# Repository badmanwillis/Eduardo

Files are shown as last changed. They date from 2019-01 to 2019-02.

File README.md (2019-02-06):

# Eduardo
Eduardo the hair combing robot. An assistive robot arm prototype featuring a passive compliant end effector. A University of Plymouth MEng Robotics ROCO504 project.

Olly Smith and Sam White 2018. Module lead by Martin F Stoelen.

## About Eduardo

People with temporary or permanent disabilities often struggle to perform daily tasks, and as a result, this loss of agency can cause undue emotional distress. For this project, we present “Eduardo”; a prototype robot arm designed with the intention of returning autonomy to the user. In particular, we utilise a passive compliant element in the end effector, to greatly simplify the control of the arm, and ensure the safety of the user during physical interaction. As a demonstration of the prototype, we have programmed the arm to comb hair, although we envision a wider range of potential applications.

From our research, this may well be the first prototype of assistive robot that features a passive compliant end effector. It was built in under three months, by two people, on a budget of £70. As a result, shortcuts were taken for the sake of creating a functioning prototype, and much of the work here does not adhere to best practices.

Sam White was responsible for the design and manufacture of the arm. This was his first project attempted using Fusion360. Parts were rapidly protoyped and developed iterativley, through 3D printing. Additional work included parts procurement, sensor testing, and building a wheatstone bridge for the flex sensor.

Olly Smith was responsible for the ROS software and c++ microcontroller code for the arm. This was his first project attempted using ROS. Addtional work included advising Sam on designing parts for 3D printing - having built an ANET A8, and creating a custom control board for the stepper drivers and servo power rails.

Finally, the robot arm itself lends itself to further use as a development platform at the university for research projects. The large workspace (including the vertical prismatic element of the pedestal), well executed construction of the arm using low cost components, and open source software, makes the arm a viable candidate for students to use in their own research projects, continuing the research we present, and for their own ideas.

## Media
imgur album

[Rough cut of a showcase video for the project](https://www.youtube.com/watch?v=7iySw0dwJq0)

## ROS packages

The software was developed on a Ubuntu 16.04 LTS machine, using ROS-Kinetic. You'll need to setup a catkin workspace, and put the packages into the src folder.

#### Setup a workspace
[Creating a Catkin Workspace](http://wiki.ros.org/catkin/Tutorials/create_a_workspace)

Open a terminal (should default to the home directory):
 
create the folders
> mkdir -p ~/eduardo_ws/src

navigate to the root folder
> cd ~/eduardo_ws/

make the workspace using the catkin_make command
> catkin_make

#### Add the packages
[Creating a ROS Package](http://wiki.ros.org/catkin/Tutorials/CreatingPackage)

Move the two folders "sam" and "sam_moveit_config" into the src folder.

Make sure you are still in the root folder "eduardo_ws" using the "cd" and "cd .." commands

re-build the workspace

> catkin_make

"source the workspace". This means adding the workspace to the ROS enviroment by sourcing the generated setup file.

> source devel/setup.bash 

### sam

This package features the Fusion360 stl files for the the arm links, as well as the samcad.urdf (Universal Robot Description Format) file. It can be used to visualize the arm in Rviz, and control the joints via GUI sliders.

#### usage
Navigate to your workspace

> cd ros_ws

Source your workspace

> source devel/setup.bash

run the demo

> roslaunch sam arm_display.launch 

Wait for Rviz to load, then use the joint_state_publisher window sliders to play about with the arm.

### sam_moveit_config

The [moveit!](https://moveit.ros.org/) configuration package for the samcad.urdf. Unfortunatley it doesn't support path planning right now, as the deafult kinematics solvers only support 6DOF arms. I've tried adding a dummy link, which should fix the issue with a bit more work.

#### usage
Navigate to your workspace

> cd ros_ws

Source your workspace

> source devel/setup.bash

run the demo

> roslaunch sam_moveit_config demo.launch

Wait for Rviz to load, tick the "Allow Approx IK Solutions" option in the Planning tab. Drag the arm Query Start State and Query Goal State (found under Planning Request), and use the commands within the Planning tab to have moveit perform path planning and simulate the arms movement.

## Motor control code

A [ST-Nucleo-F429ZI Microcontroller](https://os.mbed.com/platforms/ST-Nucleo-F429ZI/) was used to control the stepper and servo motors, as well as read the the flex sensor value.

### nucleo_code.cpp
Most complete working code. The start and end postions of the arm are hard coded, and upon excution (trigger from a ros terminal command).

### demo_code.cpp
A version of nucleo_code.cpp with all superfluous code removed. Used to demostrate the arm on the demostration day. See the simple combing demonstration for usage.

### master_code.cpp
The most complete code in developement. Unfinished. Designed to by used by both the arm_display.launch program (sam) to allow remote control from the computer, using the GUI sliders. Also for use by the demo.launch (sam_moveit_config) program to execute path planning between given positions.

#### Simple combing demonstration
For the project showcase day a greatly simplified version of the code (demo_code.cpp) was run, to ensure a successful demonstration.
**_WARNING_. The arm will move to a starting position as soon as the microcontroller and PSU are on.**

In a terminal.
> roscore

Open a new terminal tab (Ctrl + shift + T). Then run the ros serial command to connect the Ubuntu machine to the Microcontroller. If you forgot to plug the microcontroller into the computer first, that's okay, I've done it as well.
> rosrun rosserial_python serial_node.py _port:=/dev/ttyACM0 _baud:=115200

Have the arm execute a hard coded path. Place a head of hair in the path of the arm to have it combed.
> rostopic pub toggle_execute std_msgs/Empty --once

#### Other useful commands
These have proven useful in development.

List the current ROS topics
> rostopic list

Print the updating values of the joints of the arm.
> rostopic echo joint_states

Generate a ROS computation graph to visualize the topics and nodes.
> rqt_graph

## Further improvements
There is no shortage of improvements to be made to this project, and we hope to see the continued development of this arm in the future.

### Research
- Attempt combing on the sides of the hair, and potentially to style the hair.
- Create an end effector using an antagonstic pair, for variable compliance.
- Experiment with other means of helping a person with upper body impairments. Examples include washing, feeding, clothing.

### Safety
- Add microswitches to the prismatic gantry and shoulder revolute joints as endstops. Like a 3D printer.
- Add padding to the arm itself, potentially with sensors or microswithces to detect a collision.
- Add a big red emergency stop button.

### Design and construction
- An improved attachment method, which still allows for end effectors to be easily swapped. The current end effector attachement is friction fit, and can become loose over time.
- Create a better mount for the PSU and motor control board. Currently an elastic band is doing a fantastic job, but it's not ideal.
- Addition of a belt tensioner for the  shoulder joint would make keeping the belt taught much simpler.
- Replacing servo plugs with molex connectors. Current connects have no locking mechanism and can occasionally be pulled out when prismatic joint is at it's extremes.
- A comb piece design with less sharp prongs should be considered. Adjust as necessary for comfort.

### Control Software
- Intergrate a sensor to establish the cartesian position of the users head. This was attempted using a KinectV2, and a custom stereo camera system, but was abandoned due to time.
- Intergate the Stepper motor for the pedestal, adding a vertical prismatic joint to the URDF.

#### Moveit!
- Create a custom kinematics solver plugin, or use IKFast, or Trac-IK.
- Define controllers. A YAML file of the joints. See sam_moveit_config > config.
- Use python scripting to control the arm. See the [Move Group Python Interface](http://docs.ros.org/kinetic/api/moveit_tutorials/html/doc/move_group_python_interface/move_group_python_interface_tutorial.html) tutorial.

- Create a launch file / bash script that launches the whole enviroment from single terminal command

### Fun ideas
- Implement voice synthesis, give it an old-timey british barber voice, a bit like Codsworth from Fallout 4.
- Create an end effector of a silicon mould of a hand, to high-five passers by.

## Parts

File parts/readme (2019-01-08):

Parts list from Ooznest and step(.stp) CAD files for all printed parts necessary to the build of the arm.  

'Parts List' is a text document including parts bought, in what quiantity and a link to the page from which they were purchased. 

'Eduardo Step Files' is a set of step files for the CAD design.

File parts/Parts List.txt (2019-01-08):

Official List of Parts on OpenBuild
https://openbuilds.com/builds/nema-17-belt-and-pinion-system.7499/

V-Slot Gantry Plate (x1)
https://ooznest.co.uk/product/v-slot-gantry-plate/

NEMA17 Motor Mounting Plate (x1)
https://ooznest.co.uk/product/nema17-motor-mounting-plate/

Delrin Dual V Wheel Kit (x4)
https://ooznest.co.uk/product/delrin-dual-v-wheel/

Tee Nuts (x10)
https://ooznest.co.uk/product/tee-nuts/

GT2 Pulley 20T (x2)
https://ooznest.co.uk/product/gt2-pulleys/

GT2 Open Timing Belt 
https://ooznest.co.uk/product/gt2-open-timing-belt-per-metre/

V-Slot Linear Rail – 20x80x1000mm (x1)
https://ooznest.co.uk/product/v-slot-linear-rail-20x80mm-cut-to-size/

M3 Socket Head Bolts (x8)
https://ooznest.co.uk/product/m3-socket-head-bolts/

M5 Low Profile Bolts (x8)
https://ooznest.co.uk/product/low-profile-m5-bolts/

Aluminium Spacers (x2)
https://ooznest.co.uk/product/aluminium-spacer/

Eccentric Spacer (x2)
https://ooznest.co.uk/product/eccentric-spacer/

Double Tee Nut (x2)
https://ooznest.co.uk/product/double-tee-nuts/

Total at time of ordering - £73.86

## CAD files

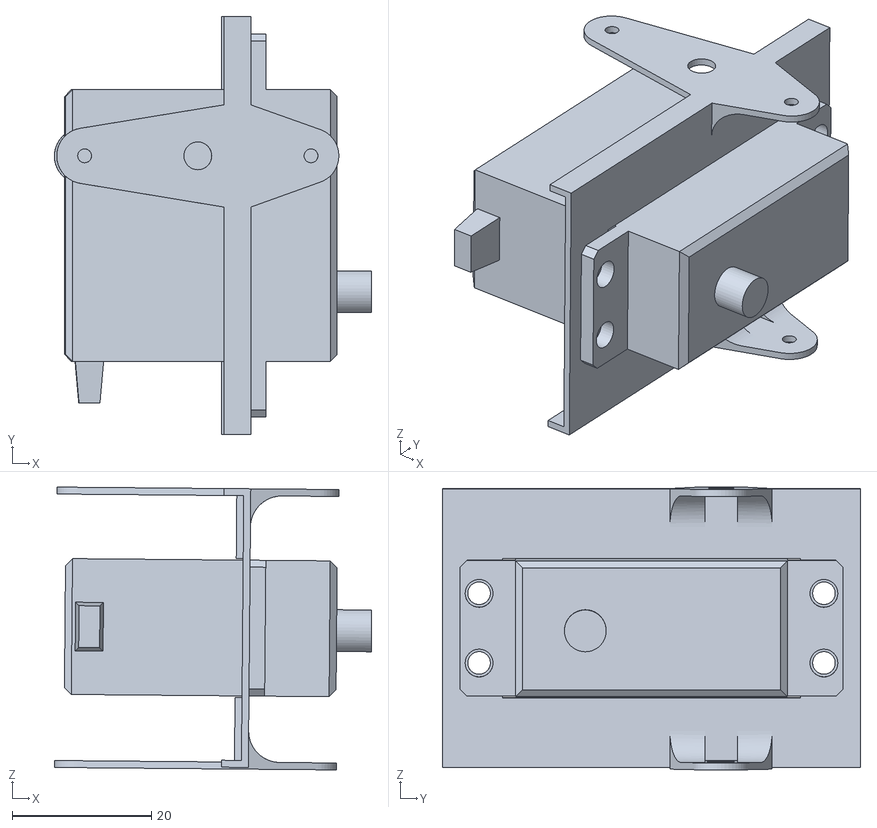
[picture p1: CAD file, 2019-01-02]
sam/src/stls/03_Wrist Servo.stl
45.5 x 60.0 x 40.6

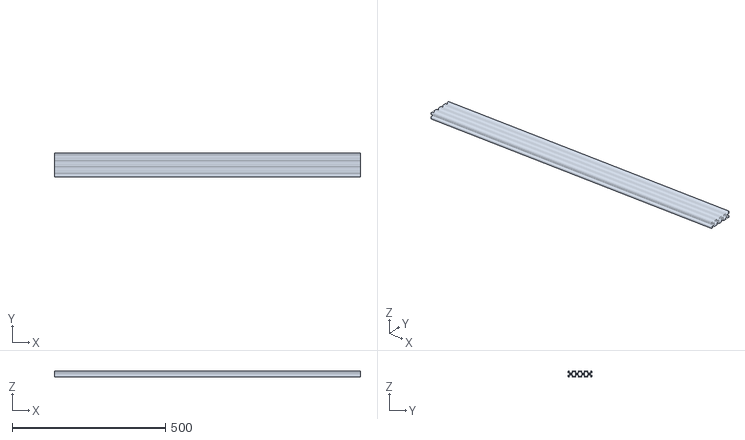
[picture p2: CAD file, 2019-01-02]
sam/src/stls/07_Rail.stl
1000.0 x 80.0 x 20.0

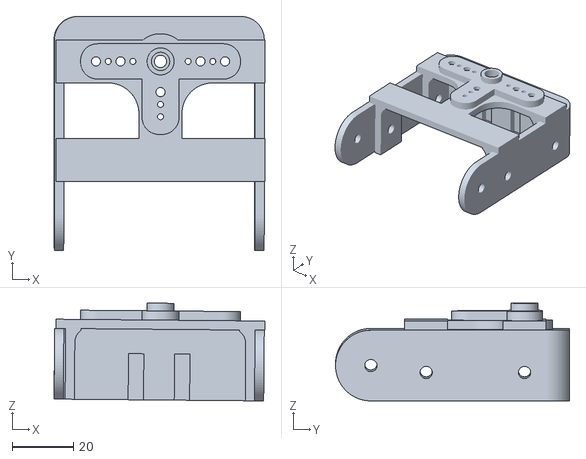
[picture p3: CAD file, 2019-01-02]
sam/src/stls/02_End Effector Front.stl
68.6 x 76.1 x 31.8

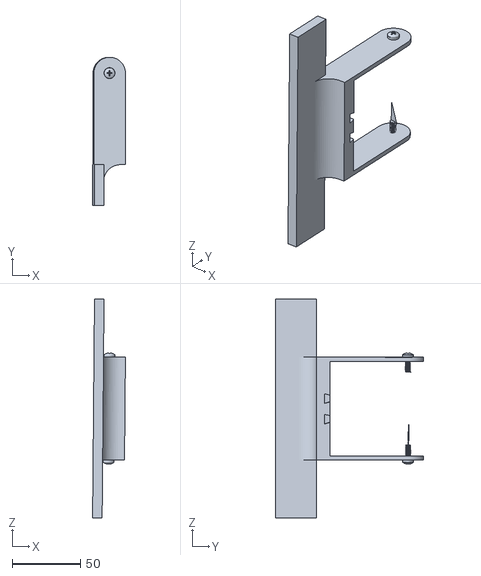
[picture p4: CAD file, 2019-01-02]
sam/src/stls/01_End Effector Top.stl
24.0 x 108.5 x 160.1

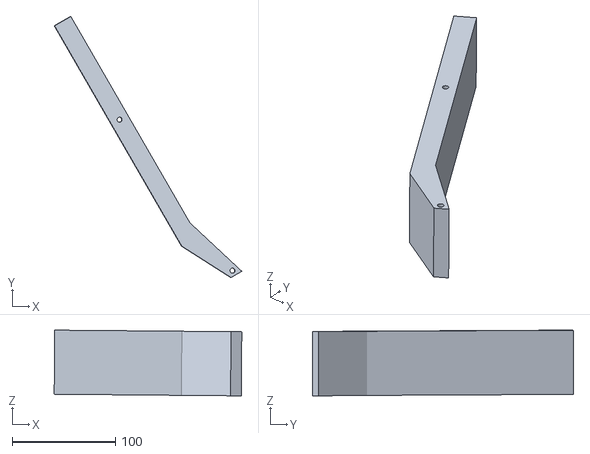
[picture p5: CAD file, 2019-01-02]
sam/src/stls/04_Forearm.stl
181.4 x 252.3 x 63.6

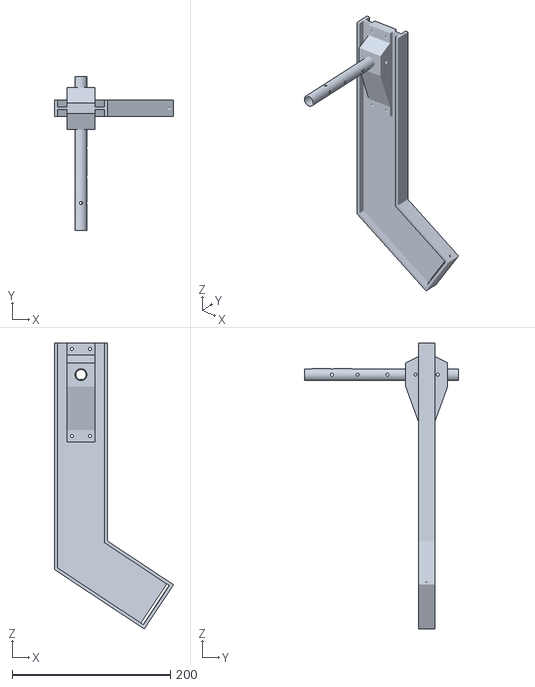
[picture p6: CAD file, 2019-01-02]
sam/src/stls/05_Upper Arm.stl
150.4 x 195.0 x 361.1

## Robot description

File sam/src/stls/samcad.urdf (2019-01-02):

<?xml version="1.0"?>

<!--
Olly Smith & Sam White 2018

Loading in fusion360 parts to create a URDF model of the robot.

-->

<robot name="eduardo">

<!--
2.1.19
fixing the kinematics via a dummy base link
https://groups.google.com/forum/#!topic/moveit-users/kQXU5NYgOF8
-->

  <link name="base_footprint">
    <visual>
      <origin rpy="0 0 0" xyz="0 0 0"/>
      <geometry>
        <box size="0.001 0.001 0.001"/>
      </geometry>
    </visual>
  </link>

  <link name="base_link">
    <visual>
      <geometry>
        <mesh filename="file:/home/olly/ros_ws/src/sam/src/stls/07_Rail.stl" scale="0.001 0.001 0.001"/>
      </geometry>
      <origin rpy = "1.57 0 0" xyz = "0 0 0.04"/>
    </visual>
  </link>


  <joint name="base_footprint_joint" type="fixed">
    <origin rpy="0 0 0" xyz="0 0 0"/>
    <child link="base_link"/>
    <parent link="base_footprint"/>
  </joint>

  <link name="shoulder">
    <visual>
      <geometry>
        <mesh filename="file:/home/olly/ros_ws/src/sam/src/stls/06_GantryPlate.stl" scale="0.001 0.001 0.001"/>
      </geometry>
      <origin rpy = "1.57 0 0" xyz = "0 0 0.04"/>
    </visual>
  </link>

  <joint name="base_to_shoulder" type="prismatic">
    <axis xyz="1 0 0"/>
    <limit effort="1000" lower="-0.45" upper="0.45" velocity="0.1"/>
    <parent link="base_link"/>
    <child link="shoulder"/>
    <origin rpy = "0 0 0" xyz = "0 0 0"/>
  </joint>

  <link name="upper_arm">
    <visual>
      <geometry>
        <mesh filename="file:/home/olly/ros_ws/src/sam/src/stls/05_Upper Arm.stl" scale="0.001 0.001 0.001"/>
      </geometry>
      <origin rpy = "1.57 0 0" xyz = "0 0 0"/>
    </visual>
  </link>


  <joint name="shoulder_upper_arm" type="revolute">
    <axis xyz="0 0 1"/>
    <limit effort="1000" lower="-1" upper="1" velocity="0.1"/>
    <parent link="shoulder"/>
    <child link="upper_arm"/>
    <origin rpy = "0 0 0" xyz = "0 0.043 0"/>
  </joint>

  <link name="lower_arm">
    <visual>
      <geometry>
        <mesh filename="file:/home/olly/ros_ws/src/sam/src/stls/04_Forearm.stl" scale="0.001 0.001 0.001"/>
      </geometry>
      <origin rpy = "0 0 0" xyz = "0 0 0"/>
    </visual>
  </link>

  <joint name="upper_lower_arm" type="revolute">
    <axis xyz="0 0 1"/>
    <limit effort="1000" lower="0.3" upper="2.5" velocity="0.1"/>
    <parent link="upper_arm"/>
    <child link="lower_arm"/>
    <origin rpy = "1.0 1.57 0" xyz = "0.093 0.29 0.1377"/>
  </joint>



  <link name="comb_upper">
    <visual>
      <geometry>
        <mesh filename="file:/home/olly/ros_ws/src/sam/src/stls/03_Wrist Servo.stl" scale="0.001 0.001 0.001"/>
      </geometry>
      <origin rpy = "0 0 0" xyz = "0 0 0"/>
    </visual>
  </link>

  <joint name="lower_arm_hand" type="revolute">
    <axis xyz="0 0 1"/>
    <limit effort="1000" lower="-0.85" upper="1.6" velocity="0.1"/>
    <parent link="lower_arm"/>
    <child link="comb_upper"/>
    <origin rpy = "0 0 0" xyz = "0.108 -0.144 0"/>
  </joint>


  <link name="comb">
    <visual>
      <geometry>
        <mesh filename="file:/home/olly/ros_ws/src/sam/src/stls/02_End Effector Front.stl" scale="0.001 0.001 0.001"/>
      </geometry>
      <origin rpy = "0 0 0" xyz = "0 0 0"/>
    </visual>
  </link>

  <joint name="comb" type="revolute">
    <axis xyz="0 0 1"/>
    <limit effort="1000" lower="-1.6" upper="1.6" velocity="0.1"/>
    <parent link="comb_upper"/>
    <child link="comb"/>
    <origin rpy = "0 -1.57 0" xyz = "0.0224 -0.0195 0"/>
  </joint>


  <link name="comb_end">
    <visual>
      <geometry>
        <mesh filename="file:/home/olly/ros_ws/src/sam/src/stls/01_End Effector Top.stl" scale="0.001 0.001 0.001"/>
      </geometry>
      <origin rpy = "0 0 0" xyz = "0 0 0"/>
    </visual>
  </link>

  <joint name="comb_end" type="revolute">
    <axis xyz="0 0 1"/>
    <limit effort="1000" lower="0" upper="1.6" velocity="0.1"/>
    <parent link="comb"/>
    <child link="comb_end"/>
    <origin rpy = "0 1.57 0" xyz = "0.0032 -0.049387 -0.01975"/>
  </joint>











































</robot>

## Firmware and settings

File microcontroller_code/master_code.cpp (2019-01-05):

#include "mbed.h"
#include "rtos.h"
#include "Servo.h"
#include "ros.h"
#include <std_msgs/Float32.h>
#include <ros.h>
#include <std_msgs/Empty.h>
#include <sensor_msgs/JointState.h>

Serial pc(USBTX, USBRX);
ros::NodeHandle nh;

DigitalOut green(LED1); //Green LED Used to indicate when nucleo has finished executing a movement.
DigitalOut blue(LED2); //Blue LED Used to indicate that the robot is moving.
DigitalOut red(LED3); // Red LED

//Stepper Motors
DigitalOut rev_step(D4); // toggle high to step one increment. //D5 on my nucleo board has a jumper pin stuck in it.
DigitalOut rev_direction(D7); //1 for forwards, 0 for backwards
DigitalOut pris_step(D6);
DigitalOut pris_direction(D8); //1 for forwards, 0 for backwards

//Servo Motors
Servo elbow(D11);
Servo wrist(D10);
Servo hand(D9);

// Flex sensor
AnalogIn   flex_A0(A0);
AnalogIn   flex_A1(A1);
float flex_delta;
float flex_total;
float flex_1;
float flex_2;
float flex_3;
float flex_4;
float flex_5;
float flex_6;
float flex_7;
float flex_8;
float flex_9;
float flex_10;


// goal positions for Servo motors, to be set by the joint_states publisher.
float elbow_goal;
float wrist_goal;
float hand_goal;


// goal positions for Stepper motors, to be set by the joint_states publisher.
int revolute_goal;
int prismatic_goal;

// Current stepper positions
int revolute_pos;
int prismatic_pos;

Thread thread;

void messageCb(const std_msgs::Empty& toggle_msg);
void messageCb1(const std_msgs::Empty& toggle_msg);


ros::Subscriber<std_msgs::Empty> sub("toggle_led", &messageCb);
ros::Subscriber<std_msgs::Empty> sub1("toggle_execute", &messageCb1);
std_msgs::Float32 flex_msg;
ros::Publisher flex("flex", &flex_msg);

 
void ros_thread() {
    while (true) {
        //red = !red;
        //Thread::wait(1000);
        nh.spinOnce();
        Thread::wait(1);
    }
}

// callback messages: Toggle LED
void messageCb(const std_msgs::Empty& toggle_msg){
    green= !green;   // blink the led
}
// callback messages: EXECUTE
int execute = 0;
void messageCb1(const std_msgs::Empty& toggle_msg){
    execute = 1;
    
    green = !green;   // blink the led
}

// joint_state subscriber
#include <sensor_msgs/JointState.h>
void jointCb(const sensor_msgs::JointState& cmd_msg)
{
    //str_msg.data = hello;
    //chatter.publish( &str_msg ); 
    //myled = !myled;
    
    // Code here to take the joint_states and put them into a means that can be used by the code to move the arm.
    // Splitting the input data, putting data into variables eg:
    
    // hand_goal = joint_states[element of array for hand joint state];
    
}
ros::Subscriber<sensor_msgs::JointState> sub2("joint_states", &jointCb);


int main() {
    
    // ROS setup
    nh.initNode();
    pc.baud (115200);
    nh.subscribe(sub);
    nh.subscribe(sub1);
    nh.subscribe(sub2); //joint_states
    nh.advertise(flex);
    thread.start(ros_thread);
    
    // initialise stepper positions to 0
    prismatic_pos =0;
    revolute_pos =0;
    //initialise servo positions to 0
    elbow   =0.5;
    wrist   =0.5;
    hand    =0.7;
    
    int step_rate = 1; // the wait time, in us. Essentially speed control for all motors.
    
    // TESTING goal positions
    prismatic_goal  =4000;
    revolute_goal   =0;
    elbow_goal      =0.5;
    wrist_goal      =0.5;
    hand_goal       =0.7;
    
    // Servo goal tolerances
    float elbow_plus = elbow_goal + 0.01f;
    float elbow_minus = elbow_goal - 0.01f;
    
    float wrist_plus = wrist_goal + 0.01f;
    float wrist_minus = wrist_goal - 0.01f;
    
    float hand_plus = hand_goal + 0.01f;
    float hand_minus = hand_goal - 0.01f;
    
    // Flex sensor upper and lower thresholds (too much force, too little force)
    float flex_high =  0.002;
    float flex_low = 0.001;
    
    
    
    while(1){
        

        while (execute == 1) {
            
            // FLEX SAMPLING
            flex_1 = flex_A0 - flex_A1;
            Thread::wait(1);
            flex_2 = flex_A0 - flex_A1;
            Thread::wait(1);
            flex_3 = flex_A0 - flex_A1;
            Thread::wait(1);
            flex_4 = flex_A0 - flex_A1;
            Thread::wait(1);
            flex_5 = flex_A0 - flex_A1;
            Thread::wait(1);
            flex_6 = flex_A0 - flex_A1;
            Thread::wait(1);
            flex_7 = flex_A0 - flex_A1;
            Thread::wait(1);
            flex_8 = flex_A0 - flex_A1;
            Thread::wait(1);
            flex_9 = flex_A0 - flex_A1;
            Thread::wait(1);
            flex_10 = flex_A0 - flex_A1;
        
            
            flex_total = flex_1 + flex_2 + flex_3 + flex_4 + flex_5 + flex_6 + flex_7 + flex_8 + flex_9 + flex_10;
            flex_delta = flex_total / 10;
            
            flex_delta = fabs(flex_delta);
            
            if(flex_delta < flex_low){
                // TO LOW
                red=1;
                blue=0;
                elbow = elbow - 0.003f;
                wait_ms(step_rate);
                red=0;
            } else if(flex_delta > flex_high){
                // TOO HIGH
                red=0;
                blue=1;
                elbow = elbow + 0.003f;
                wait_ms(step_rate);
                blue = 0;
            }
            

            // Check all motors have reached goal positions. IDGAF about how long the condition statement is.
            if(prismatic_pos == prismatic_goal && revolute_pos == revolute_goal && elbow <= elbow_plus && elbow >= elbow_minus && wrist <= wrist_plus && wrist >= wrist_minus && hand <= hand_plus && hand >= hand_minus){
                // goal reached
                green = 0;
                execute = 0;
                
                //reset positions, may not be needed with moveit intergration.
                prismatic_pos = 0;
                revolute_pos = 0;
            }  
            
            // ELBOW
            if(elbow < elbow_goal){
                blue=1;
                elbow = elbow + 0.01f;
                wait_us(step_rate);
                blue=0;
            } else if(elbow > elbow_goal){
                blue=1;
                elbow = elbow - 0.01f;
                wait_us(step_rate);
                blue=0;
            }
            
           
            // WRIST
            if(wrist < wrist_goal){
                blue=1;
                wrist = wrist + 0.01f;
                wait_us(step_rate);
                blue=0;
            } else if(wrist > wrist_goal){
                blue=1;
                wrist = wrist - 0.01f;
                wait_us(step_rate);
                blue=0;
            }
        
            // HAND
            if(hand < hand_goal){
                blue=1;
                hand = hand + 0.01f;
                wait_us(step_rate);
                blue=0;
            } else if(hand > hand_goal){
                blue=1;
                hand = hand - 0.01f;
                wait_us(step_rate);
                blue=0;
            }
            
            // PRISMATIC
            if(prismatic_pos < prismatic_goal){
                // step fwd 1
                pris_direction = 1;
                
                // STEP
                blue=1;
                pris_step = 1;
                wait_us(step_rate);
                blue=0;
                pris_step = 0;
                wait_us(step_rate);
                // Increment current position
                prismatic_pos +=1;
                 
            } else if(prismatic_pos > prismatic_goal){
                // step back 1
                pris_direction = 0;
                
                // STEP
                blue=1;
                pris_step = 1;
                wait_us(step_rate);
                blue=0;
                pris_step = 0;
                wait_us(step_rate);
                // Decrement current position
                prismatic_pos -=1;
                
            } else if(revolute_pos == revolute_goal){
                // to keep the speeds roughly the same
                wait_us(step_rate);
                wait_us(step_rate);
            }
            
            // REVOLUTE
            if(revolute_pos < revolute_goal){
                // step fwd 1
                rev_direction = 1;
                
                // STEP
                blue=1;
                rev_step = 1;
                wait_us(step_rate);
                blue=0;
                rev_step = 0;
                wait_us(step_rate);
                // Increment current position
                revolute_pos +=1;
                 
            } else if(revolute_pos > revolute_goal){
                // step back 1
                rev_direction = 0;
                
                // STEP
                blue=1;
                rev_step = 1;
                wait_us(step_rate);
                blue=0;
                rev_step = 0;
                wait_us(step_rate);
                // Decrement current position
                revolute_pos -=1;
                
            } else if(revolute_pos == revolute_goal){
                // to keep the speeds roughly the same
                wait_us(step_rate);
                wait_us(step_rate);
            }
            
        }
    }
    
}

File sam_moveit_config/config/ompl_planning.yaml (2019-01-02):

planner_configs:
  SBL:
    type: geometric::SBL
    range: 0.0  # Max motion added to tree. ==> maxDistance_ default: 0.0, if 0.0, set on setup()
  EST:
    type: geometric::EST
    range: 0.0  # Max motion added to tree. ==> maxDistance_ default: 0.0, if 0.0 setup()
    goal_bias: 0.05  # When close to goal select goal, with this probability. default: 0.05
  LBKPIECE:
    type: geometric::LBKPIECE
    range: 0.0  # Max motion added to tree. ==> maxDistance_ default: 0.0, if 0.0, set on setup()
    border_fraction: 0.9  # Fraction of time focused on boarder default: 0.9
    min_valid_path_fraction: 0.5  # Accept partially valid moves above fraction. default: 0.5
  BKPIECE:
    type: geometric::BKPIECE
    range: 0.0  # Max motion added to tree. ==> maxDistance_ default: 0.0, if 0.0, set on setup()
    border_fraction: 0.9  # Fraction of time focused on boarder default: 0.9
    failed_expansion_score_factor: 0.5  # When extending motion fails, scale score by factor. default: 0.5
    min_valid_path_fraction: 0.5  # Accept partially valid moves above fraction. default: 0.5
  KPIECE:
    type: geometric::KPIECE
    range: 0.0  # Max motion added to tree. ==> maxDistance_ default: 0.0, if 0.0, set on setup()
    goal_bias: 0.05  # When close to goal select goal, with this probability. default: 0.05
    border_fraction: 0.9  # Fraction of time focused on boarder default: 0.9 (0.0,1.]
    failed_expansion_score_factor: 0.5  # When extending motion fails, scale score by factor. default: 0.5
    min_valid_path_fraction: 0.5  # Accept partially valid moves above fraction. default: 0.5
  RRT:
    type: geometric::RRT
    range: 0.0  # Max motion added to tree. ==> maxDistance_ default: 0.0, if 0.0, set on setup()
    goal_bias: 0.05  # When close to goal select goal, with this probability? default: 0.05
  RRTConnect:
    type: geometric::RRTConnect
    range: 0.0  # Max motion added to tree. ==> maxDistance_ default: 0.0, if 0.0, set on setup()
  RRTstar:
    type: geometric::RRTstar
    range: 0.0  # Max motion added to tree. ==> maxDistance_ default: 0.0, if 0.0, set on setup()
    goal_bias: 0.05  # When close to goal select goal, with this probability? default: 0.05
    delay_collision_checking: 1  # Stop collision checking as soon as C-free parent found. default 1
  TRRT:
    type: geometric::TRRT
    range: 0.0  # Max motion added to tree. ==> maxDistance_ default: 0.0, if 0.0, set on setup()
    goal_bias: 0.05  # When close to goal select goal, with this probability? default: 0.05
    max_states_failed: 10  # when to start increasing temp. default: 10
    temp_change_factor: 2.0  # how much to increase or decrease temp. default: 2.0
    min_temperature: 10e-10  # lower limit of temp change. default: 10e-10
    init_temperature: 10e-6  # initial temperature. default: 10e-6
    frountier_threshold: 0.0  # dist new state to nearest neighbor to disqualify as frontier. default: 0.0 set in setup()
    frountierNodeRatio: 0.1  # 1/10, or 1 nonfrontier for every 10 frontier. default: 0.1
    k_constant: 0.0  # value used to normalize expresssion. default: 0.0 set in setup()
  PRM:
    type: geometric::PRM
    max_nearest_neighbors: 10  # use k nearest neighbors. default: 10
  PRMstar:
    type: geometric::PRMstar
  FMT:
    type: geometric::FMT
    num_samples: 1000  # number of states that the planner should sample. default: 1000
    radius_multiplier: 1.1  # multiplier used for the nearest neighbors search radius. default: 1.1
    nearest_k: 1  # use Knearest strategy. default: 1
    cache_cc: 1  # use collision checking cache. default: 1
    heuristics: 0  # activate cost to go heuristics. default: 0
    extended_fmt: 1  # activate the extended FMT*: adding new samples if planner does not finish successfully. default: 1
  BFMT:
    type: geometric::BFMT
    num_samples: 1000  # number of states that the planner should sample. default: 1000
    radius_multiplier: 1.0  # multiplier used for the nearest neighbors search radius. default: 1.0
    nearest_k: 1  # use the Knearest strategy. default: 1
    balanced: 0  # exploration strategy: balanced true expands one tree every iteration. False will select the tree with lowest maximum cost to go. default: 1
    optimality: 1  # termination strategy: optimality true finishes when the best possible path is found. Otherwise, the algorithm will finish when the first feasible path is found. default: 1
    heuristics: 1  # activates cost to go heuristics. default: 1
    cache_cc: 1  # use the collision checking cache. default: 1
    extended_fmt: 1  # Activates the extended FMT*: adding new samples if planner does not finish successfully. default: 1
  PDST:
    type: geometric::PDST
  STRIDE:
    type: geometric::STRIDE
    range: 0.0  # Max motion added to tree. ==> maxDistance_ default: 0.0, if 0.0, set on setup()
    goal_bias: 0.05  # When close to goal select goal, with this probability. default: 0.05
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

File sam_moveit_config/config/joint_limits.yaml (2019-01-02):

# joint_limits.yaml allows the dynamics properties specified in the URDF to be overwritten or augmented as needed
# Specific joint properties can be changed with the keys [max_position, min_position, max_velocity, max_acceleration]
# Joint limits can be turned off with [has_velocity_limits, has_acceleration_limits]
joint_limits:
  base_to_shoulder:
    has_velocity_limits: true
    max_velocity: 0.1
    has_acceleration_limits: false
    max_acceleration: 0
  comb:
    has_velocity_limits: true
    max_velocity: 0.1
    has_acceleration_limits: false
    max_acceleration: 0
  lower_arm_hand:
    has_velocity_limits: true
    max_velocity: 0.1
    has_acceleration_limits: false
    max_acceleration: 0
  shoulder_upper_arm:
    has_velocity_limits: true
    max_velocity: 0.1
    has_acceleration_limits: false
    max_acceleration: 0
  upper_lower_arm:
    has_velocity_limits: true
    max_velocity: 0.1
    has_acceleration_limits: false
    max_acceleration: 0

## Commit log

2019-01-02 added CAD stls and URDF
    [01_End Effector Top.stl, 02_End Effector Front.stl, 03_Wrist Servo.stl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]
2019-01-02 Uploaded sam package, featuring CAD stls and URDF
    [01_End Effector Top.stl, 02_End Effector Front.stl, 03_Wrist Servo.stl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]
2019-01-02 uploaded sam_moveit_config package
    [fake_controllers.yaml, joint_limits.yaml, ros_controllers.yaml]
